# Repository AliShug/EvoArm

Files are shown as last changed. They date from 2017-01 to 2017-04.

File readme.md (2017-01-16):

EvoArm is an open-source, 3D-printable, desktop-sized, 3+2DOF robot arm design which uses serially controlled Dynamixel smart servos. It is based in part on the [LiteArm i2](http://www.thingiverse.com/thing:480446) design by "Armatec".

[Licensed under CC-BY-SA 3.0](https://creativecommons.org/licenses/by/3.0/)

## Core Action
Swing | Main Arm | Actuator/Forearm
--- | --- | ---
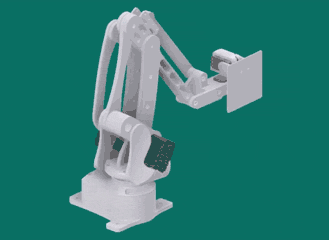
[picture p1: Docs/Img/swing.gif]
Swing GIF
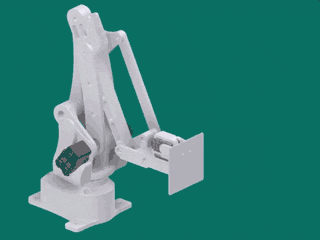
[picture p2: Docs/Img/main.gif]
Main GIF
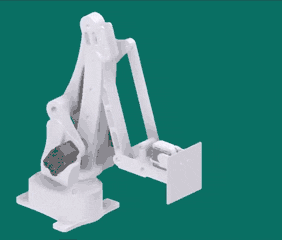
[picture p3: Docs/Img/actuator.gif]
Actuator GIF
 |  | 

The arm is actuated using 3 Dynamixel smart servos, either the [AX-12 or 18A](http://support.robotis.com/en/product/actuator/dynamixel/dxl_ax_main.htm), which both have identical casings and control protocols - I recommend using AX-18A motors, as the 12s are a bit underpowered.

## Effector
The design presented here has a flat touchpad actuated using 2 Dynamixel [XL-320](http://support.robotis.com/en/product/actuator/dynamixel_x/xl_series/xl-320.htm) servos, providing an additional 2DOF at the arm's "wrist". The design inherently keeps the base wrist joint level with the floor.

## Inverse Kinematics
The inverse kinematics application is written in Python with [PyGame](http://pygame.org/hifi.html), and takes the form of a graphical control app which also accepts simple streamed commands from other programs via UDP. It serves the purpose of calculating the desired target servo positions for the arm, given a 3D target position and orientation for the end-effector. It also provides linear interpolation on the target position and basic bounds-checking to prevent self-interference on the motors or mechanical failure of the design (the reachable volume is visualised in green).

Start the application with `python PyIK` from the root directory. Unfortunately the application may not be usable on smaller screens, since the size is fixed. To enable control, press the spacebar, and watch the command window in which the app was started for additional information.

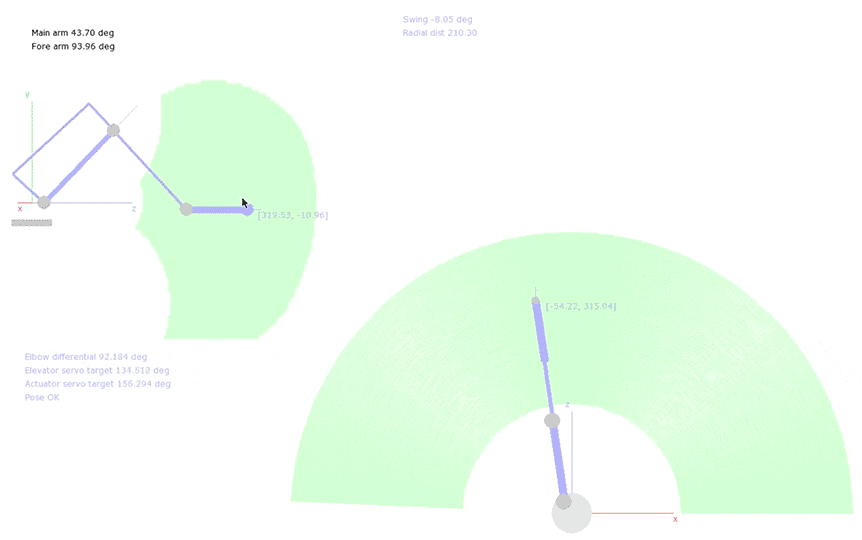
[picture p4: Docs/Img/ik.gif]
Inverse Kinematics program


The IK app is configured to connect to the arm through a properly configured Arduino Mega2560 controller, from a Windows machine. More details to come!

## Hardware
The current system interfaces with the servos using an Arduino Mega2560, which provides multiple hardware UARTs in addition to the one used for PC/Arduino communications. The AX and XL series servos use different control protocols, so they are connected to the Arduino on physically separate lines, with one UART Tx/Rx pair for each *set* of servos. Since the servos use only a single (synchronous) data line, the Tx/Rx lines are multiplexed using a 74LS241 tri-state buffer. The multiplexing is controlled using an additional transmit enable line from the Arduino.

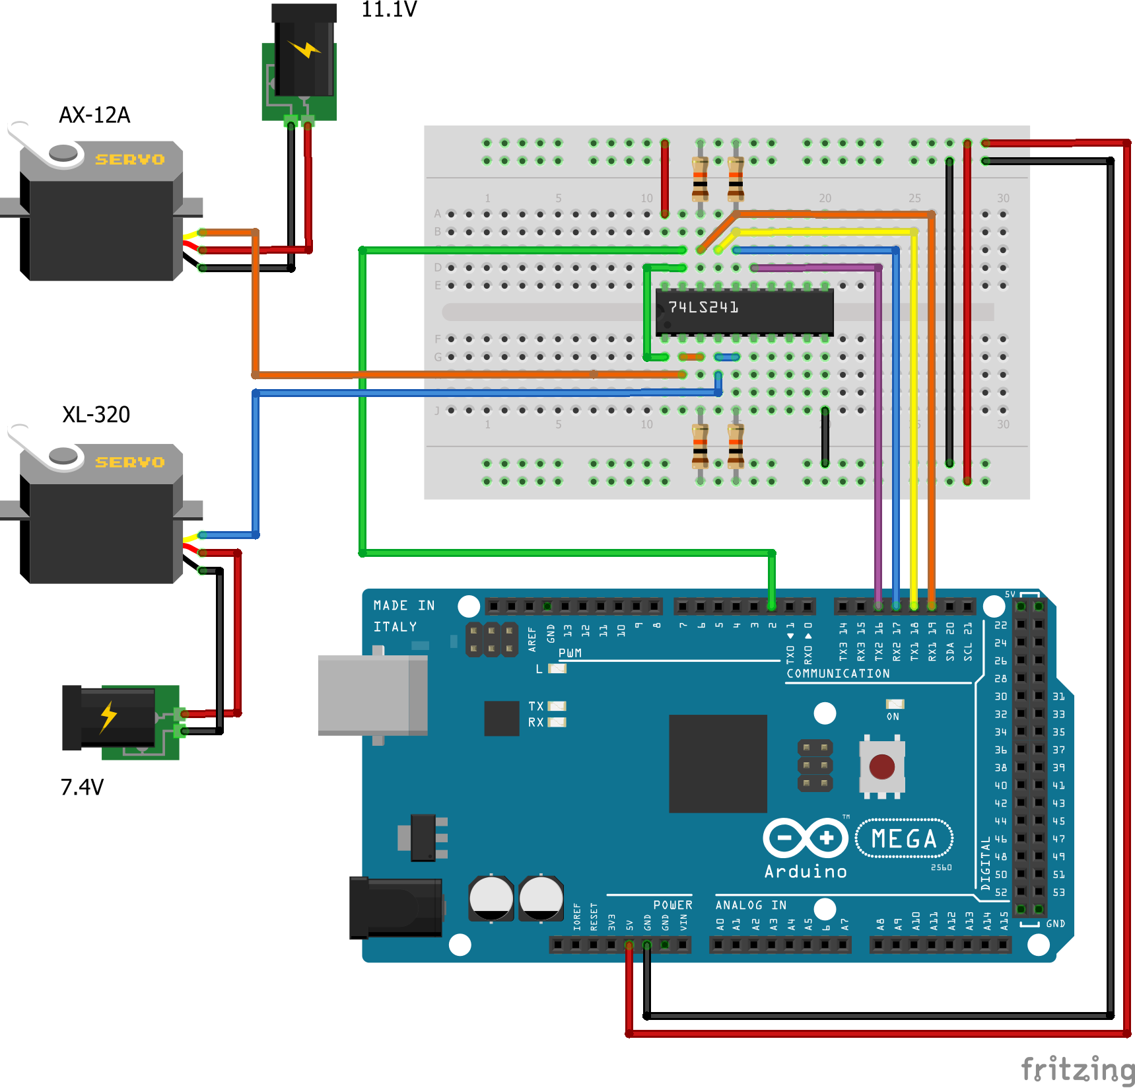
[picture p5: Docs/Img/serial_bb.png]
Breadboard diagram of hardware


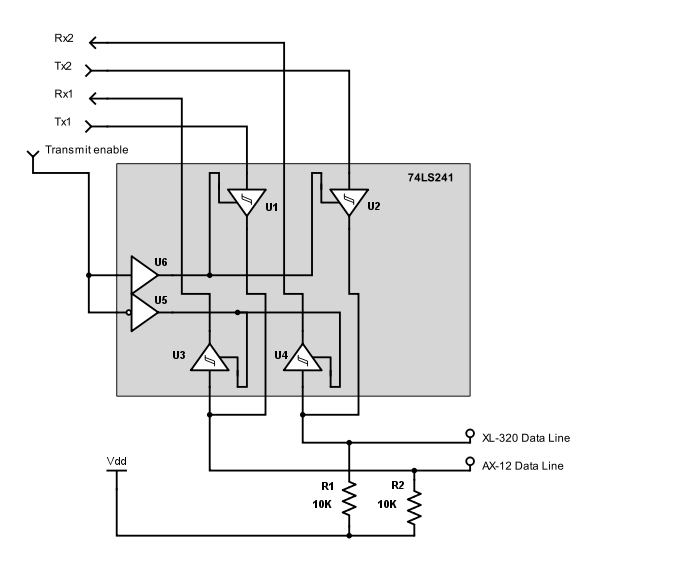
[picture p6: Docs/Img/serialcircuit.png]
Circuit diagram of serial communications
  

The data lines should be pulled high (to +5V) to stop them from "floating" while not in use.

Experimentally, it's possible to interface with these servos using only an Arduino Uno (or equivalent, e.g. Arduino Nano), without preventing the use of the single hardware UART for PC/Arduino communications. The ATMega328p in those boards is clocked high enough to allow basic *software-based* synchronous serial at 1 megabaud, using only one pin for each data line, and *no additional hardware*. The downside is interfering with the interrupts on the board, which can break some of the normal Arduino timing routines. If all you want to do is communicate with the servos from a PC, this doesn't matter. I'll explore this option further when I have the chance.

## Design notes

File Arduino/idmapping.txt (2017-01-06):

ModelNumber : 0x00
FirmwareVersion : 0x01
ID : 0x02
ReturnDelay : 0x03
CWLimit : 0x04
CCWLimit : 0x05
TempLimit : 0x06
LowVoltageLimit : 0x07
HighVoltageLimit : 0x08
MaxTorque : 0x09
MaxTorque : 0x0A
AlarmFlags : 0x0B
ShutdownFlags : 0x0C
TorqueEnable : 0x0D
LED : 0x0E
Voltage : 0x0F
Position : 0x10
Load : 0x11
Temperature : 0x12
Speed : 0x13
GoalPosition : 0x14
GoalSpeed : 0x15
TorqueLimit : 0x16
CWMargin : 0x17
CCWMargin : 0x18
CWSlope : 0x19
CCWSlope : 0x1A
Punch : 0x1B
Moving : 0x1C

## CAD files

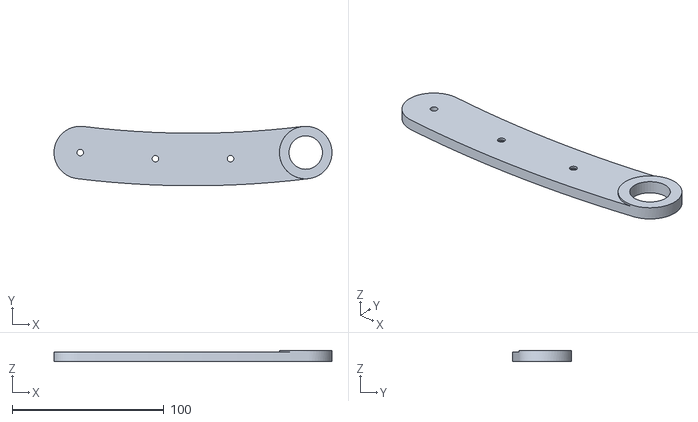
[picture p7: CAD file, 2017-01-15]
Design/Arm - main arm R.stl
183.0 x 39.1 x 7.00

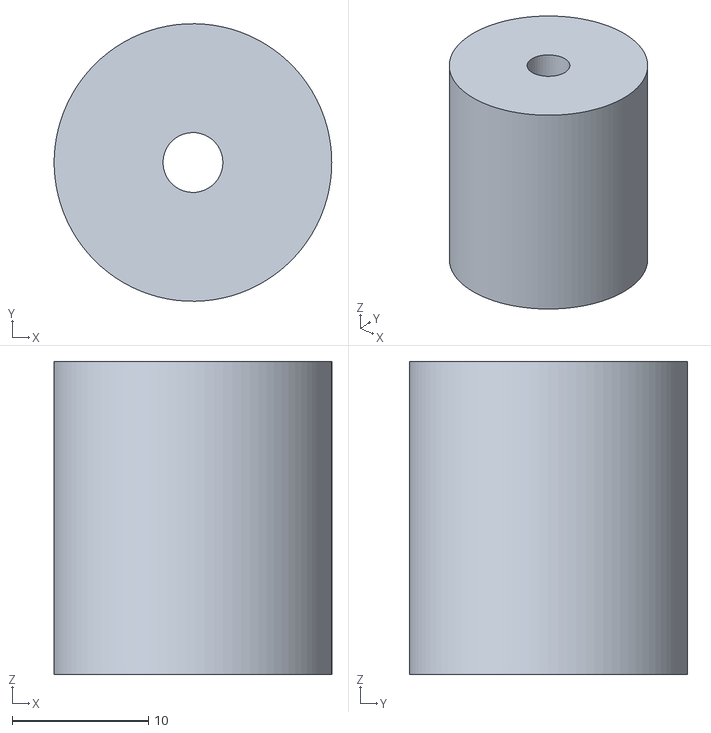
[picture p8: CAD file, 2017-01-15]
Design/Arm - main arm spacer.stl
20.4 x 20.4 x 23.0

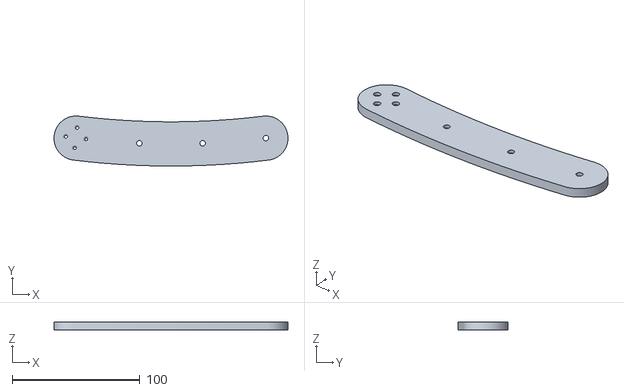
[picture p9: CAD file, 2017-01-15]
Design/Arm - main arm L.stl
183.0 x 39.1 x 6.00

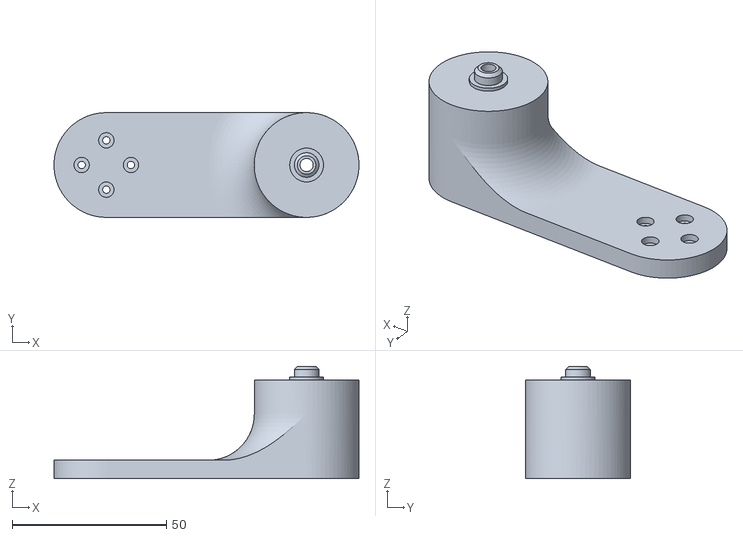
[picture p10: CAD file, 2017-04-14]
Design/Arm - actuator hinge R.stl
99.0 x 34.0 x 36.5

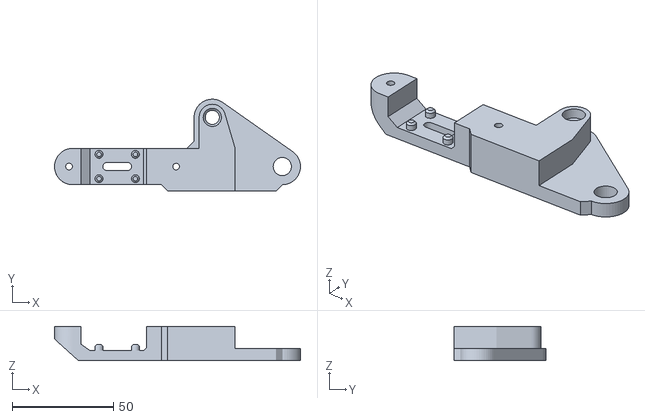
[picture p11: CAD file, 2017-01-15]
Design/Derived Parts/Arm - effector right v2.stl
121.6 x 45.3 x 17.0

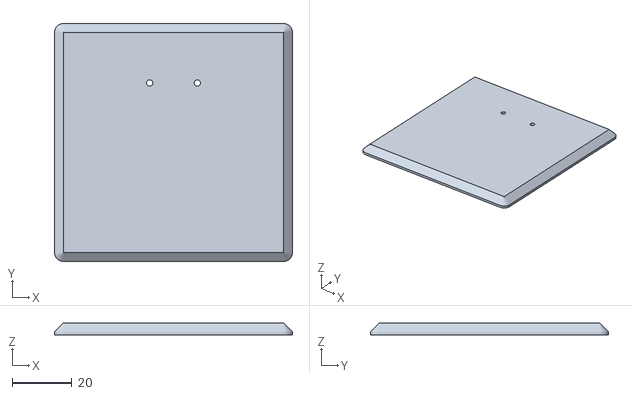
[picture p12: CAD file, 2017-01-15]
Design/Effector/Touchplate.stl
80.0 x 80.0 x 4.00

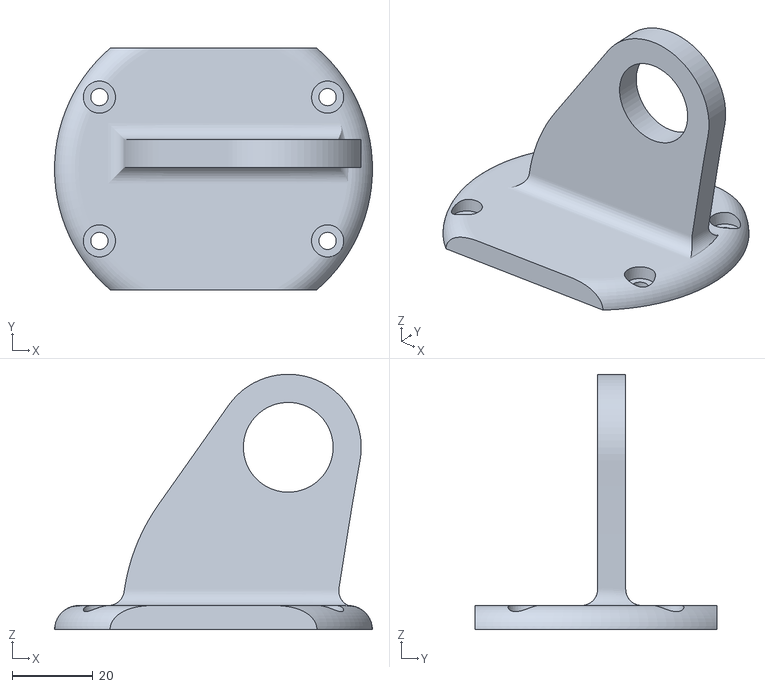
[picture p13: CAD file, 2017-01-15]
Design/Arm - base center support.stl
79.0 x 60.0 x 63.4

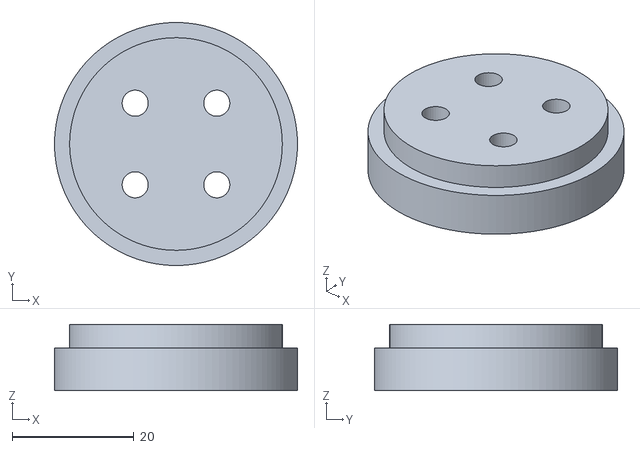
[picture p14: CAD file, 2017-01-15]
Design/Derived Parts/Base Shaft.stl
40.0 x 40.0 x 10.9

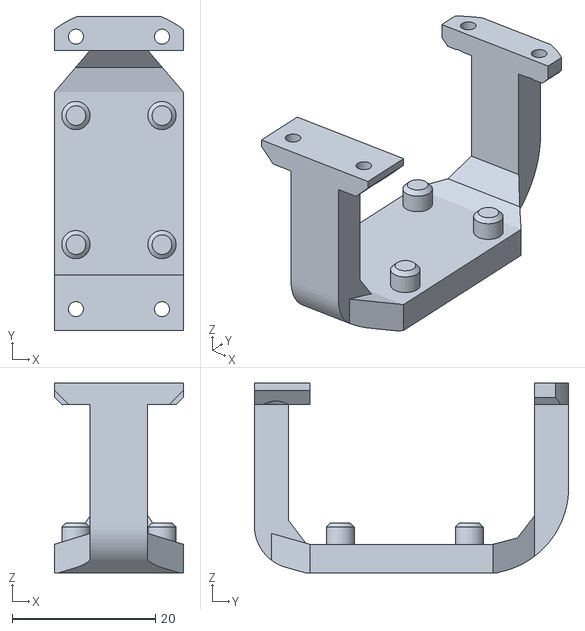
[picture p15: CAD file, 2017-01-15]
Design/Effector/Joint Upper.stl
18.0 x 43.8 x 26.5

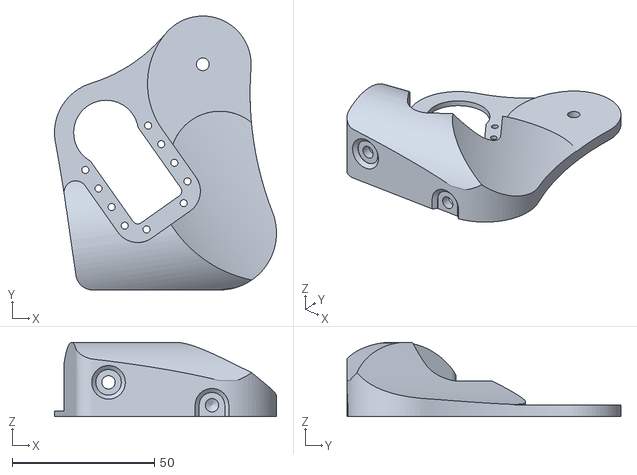
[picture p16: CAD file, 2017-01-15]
Design/Arm - shoulder L.stl
78.0 x 96.3 x 26.1

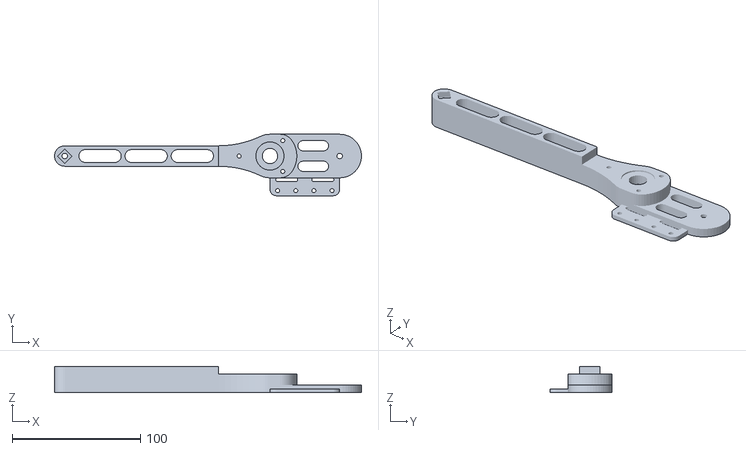
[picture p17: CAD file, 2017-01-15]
Design/Derived Parts/Arm - forearm v2 1.stl
239.4 x 48.0 x 20.6

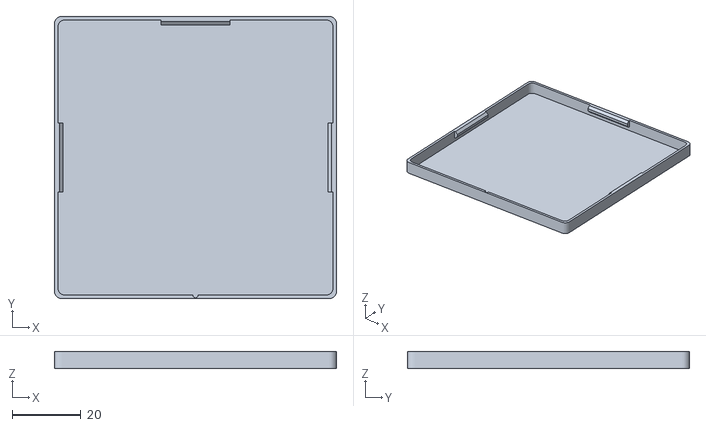
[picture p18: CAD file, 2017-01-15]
Design/Effector/Cap plate.stl
82.0 x 82.0 x 5.00

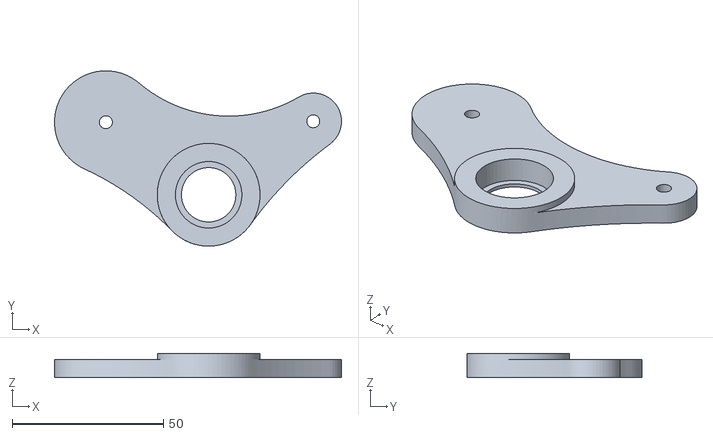
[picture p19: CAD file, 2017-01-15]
Design/Arm - parallel hinge.stl
94.9 x 58.0 x 8.00

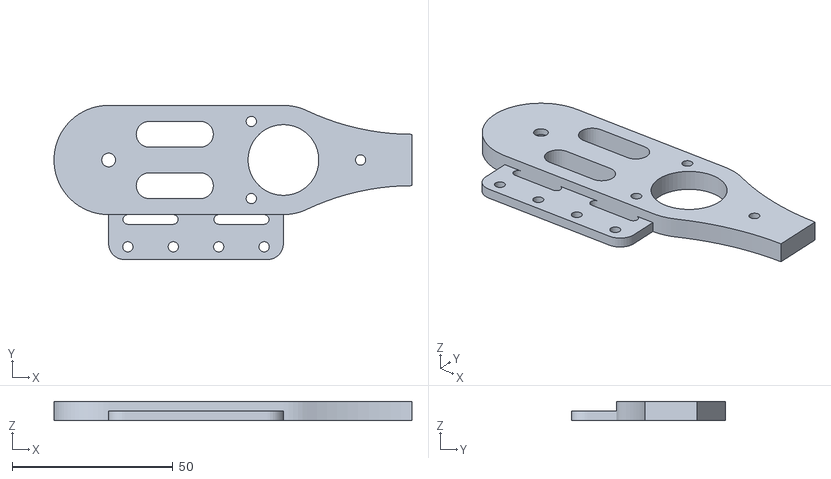
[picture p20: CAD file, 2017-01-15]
Design/Derived Parts/Arm - forearm v2 2.stl
111.4 x 48.0 x 6.00

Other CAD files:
Design/Effector/Joint Lower.stl
Design/Arm - actuator linkage.stl
Design/Derived Parts/Base Plate.stl
Design/Derived Parts/Effector - Hinge 1.stl
Design/Arm - 608 bearing cap [Med].ipt
Design/Arm - 608 bearing cap [Med].stl
Design/Arm - 608 bearing cap [Small].ipt
Design/Arm - 608 bearing cap [Small].stl
Design/Arm - actuator hinge L.ipt
Design/Arm - actuator hinge L.stl
Design/Arm - actuator hinge R.ipt
Design/Arm - actuator linkage.ipt
Design/Arm - base center support.ipt
Design/Arm - effector base v2.ipt
Design/Arm - effector hinge.ipt
Design/Arm - effector joint.ipt
Design/Arm - forearm v2 hinge.ipt
Design/Arm - forearm v2 hinge.stl
Design/Arm - forearm v2.ipt
Design/Arm - main arm L.ipt
Design/Arm - main arm R.ipt
Design/Arm - main arm spacer.ipt
Design/Arm - mounting bottom.ipt
Design/Arm - mounting bottom.stl
Design/Arm - mounting top.ipt
Design/Arm - mounting top.stl
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

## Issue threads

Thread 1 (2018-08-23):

Error Regarding File PyIK.py from PyIk/src/PyIK.py

nayanleo, 2018-08-23:
hie AliShug,
       I refered your code and trying to use in my system(UBUNTU 14.04). when I compile PyIK.py file  I'm getting Error as follows:

No 'Logs/' folder available: Performance logging disabled
Warning: shoulder servo not connected
Warning: elbow servo not connected
Warning: wrist_y servo not connected
Warning: wrist_x servo not connected
Warning: swing servo not connected
Rendering reachable volume...
Note: Spacebar toggles movement enable/disable
Traceback (most recent call last):
  File "PyIK.py", line 413, in <module>
    app.tick()
  File "PyIK.py", line 361, in tick
    self.tickComms()
  File "PyIK.py", line 223, in tickComms
    self.sockOut.send(self.arm.getIKPose().serialize() + sensor)
socket.error: [Errno 111] Connection refused

since i'm trying to solve these errors but can you please explain why this happens.
 Regards me,
As early as possible.

Closed 2018-08-30.

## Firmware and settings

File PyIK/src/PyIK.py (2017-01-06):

from __future__ import print_function

import sys
import time
import serial
import socket
import select
import struct

import numpy as np
import pygame as pyg

from pid import PIDControl
import Protocol
from solvers import IKSolver, PhysicalSolver
import window
import views
import litearm
import capsense
import armvolume

from util import *

RECV_PORT = 14001
TRAN_PORT = 14002

MAX_SPEED = 800.0
ACCEL = 1600.0
DECEL = 1.0

CS_PORT = 'COM4'

WINDOW_W = 1280
WINDOW_H = 800

import pdb;

class Kinectics:
    def findSerial(self):
        ports = ['COM{0}'.format(i+1) for i in range(256)]
        results = []
        for port in ports:
            try:
                comm = serial.Serial(port)
                comm.close()
                results.append(port)
            except (OSError, serial.SerialException):
                pass
        if len(results) > 0:
            return results[0]
        else:
            print ("No valid serial port found")
            return None

    def connectController(self):
        port = 'COM3'
        try:
            return Protocol.serialConnect(port, 250000)
        except:
            return None

    def findServos(self, comm):
        """Retrieves and processes the list of available (responsive) servos
        attached to the arm's Arduino controller. Returns a dictionary mapping
        from servo functions to Servo() objects, or None if no matching servo
        was found for a particular function"""
        servos = {
            'swing': None,
            'actuator': None,
            'shoulder': None,
            'wrist_x': None,
            'wrist_y': None
        }
        # Mapping of IDs->functions
        v1_IDs = {
            0 : 'swing',
            1 : 'actuator',
            2 : 'shoulder'
        }
        v2_IDs = {
            1 : 'wrist_x',
            0 : 'wrist_y'
        }
        # Servos retrieved from Arduino
        found = Protocol.findServos(comm)
        i = 0
        for v1servo in found['v1']:
            servos[v1_IDs[i]] = v1servo
            i += 1
        j = 0
        for v2servo in found['v2']:
            servos[v2_IDs[j]] = v2servo
            j += 1
        # Return our output servo dictionary
        return servos

    def __init__(self):
        self.stopped = False

        # Bind our comms socket
        self.bindSocket()

        # Performance tracking
        self.ik_time_accum = 0
        self.ik_time_counter = 0
        self.render_time_accum = 0
        self.render_time_counter = 0
        self.serial_time_accum = 0
        self.serial_time_counter = 0
        try:
            self.perflog = open('Logs/{0}.perflog'.format(time.time()), 'w')
        except IOError as e:
            print("No 'Logs/' folder available: Performance logging disabled")
            self.perflog = None
        self.time_start = time.clock()

        # Find the available servos through the attached board
        comm = self.connectController()
        self.servos = self.findServos(comm)


        window.InitRenderer()
        self.r = window.Renderer(pyg.display.set_mode([WINDOW_W, WINDOW_H], pyg.DOUBLEBUF|pyg.HWSURFACE))
        pyg.display.set_caption("IK Control Test")

        # The arm's controller - encapsulates IK and arm control
        self.arm = litearm.ArmController(
            servo_swing = self.servos['swing'],
            servo_shoulder = self.servos['shoulder'],
            servo_elbow = self.servos['actuator'],
            servo_wrist_x = self.servos['wrist_x'],
            servo_wrist_y = self.servos['wrist_y'],
            # use the default config
            arm_config = litearm.ArmConfig())

        # Capacitive sensor on connected UNO
        try:
            self.capSense = capsense.CapacitiveSensor(CS_PORT)
        except serial.SerialException as ex:
            self.capSense = None;

        self.sideView = views.PlaneView(width=10)
        self.realSideView = views.PlaneView(width=5, color=gray, positioning='offset')
        self.topView = views.TopView(width=12)
        self.realTopView = views.TopView(width=6, color=gray, positioning='offset')

        self.arm.pollServos()
        realPose = self.arm.getRealPose()
        if realPose is not None:
            self.curGoal = self.arm.getRealPose().effector
        else:
            self.curGoal = np.array([0., 50., 200.])
        self.ikTarget = np.array(self.curGoal)
        self.lastValidGoal = np.array(self.curGoal)
        self.curDir = [0.0, 0.0]
        self.goalNormal = [0, 0, 1]
        self.ikOffset = np.array([0.,0.,0.])

        self.lerpSpeed = 0
        self.lerpTimer = time.clock()
        self.lastPose = None

        # render the reachable area
        print("Rendering reachable volume...")
        self.reachableVolume = armvolume.ArmVolume(self.arm)
        self.sideView.renderReachableVolume(self.reachableVolume)

        print("Note: Spacebar toggles movement enable/disable")

    def stop(self):
        self.arm.enableMovement(False)
        if self.perflog is not None:
            self.perflog.write('ik_avg {0}\n'.format(self.ik_time_accum/self.ik_time_counter))
            self.perflog.write('serial_avg {0}\n'.format(self.serial_time_accum/self.serial_time_counter))
            self.perflog.write('render_avg {0}\n'.format(self.render_time_accum/self.render_time_counter))
            self.perflog.write('runtime {0}\n'.format(time.clock()-self.time_start))
            self.perflog.close()
        self.sockIn.close()
        self.sockOut.close()
        pyg.quit()
        self.stopped = True;

    def bindSocket(self):
        # We use UDP (datagrams) since we don't really care if the messages
        # arrive - just transmit and hope for the best
        self.sockIn = socket.socket(socket.AF_INET, socket.SOCK_DGRAM)
        self.sockOut = socket.socket(socket.AF_INET, socket.SOCK_DGRAM)
        self.sockIn.bind(('localhost', RECV_PORT))
        self.sockOut.connect(('localhost', TRAN_PORT))

    def tickComms(self):
        """(Socket comms) Check for incoming datagrams and send our updates"""
        while len(select.select([self.sockIn],[],[],0)[0]) > 0:
            # Ready to receive
            try:
                raw = self.sockIn.recv(4096)
                data = struct.unpack('?ffffff', raw)
                # enable or disable the physical arm
                # goal change is only applied with an enabled packet
                self.arm.enableMovement(data[0])
                if data[0]:
                    goalPos = np.array(data[1:4])
                    self.goalNormal = np.array(data[4:])
                    #print(data)
                    newGoal = goalPos*1000
                    self.curGoal = np.array(newGoal)
            except socket.error as err:
                print ("Socket error: {0}".format(err))
        #sensor = struct.pack('i', 0)
        if self.capSense:
            self.capSense.updateReadings()
            val = self.capSense.latest()
            try:
                sensor = struct.pack('i', int(self.capSense.latest()))
            except:
                sensor = '\0\0\0\0'
        else:
            sensor = '\0\0\0\0'
        realPose = self.arm.getRealPose()
        if realPose is not None:
            self.sockOut.send(realPose.serialize() + sensor)
        else:
            self.sockOut.send(self.arm.getIKPose().serialize() + sensor)

    def resetIKTarget(self, target):
        # Reset lerp timer
        self.lerpTimer = time.clock()
        # Reset lerp speed to 0
        self.lerpSpeed = 0.0
        # Clear error buildup
        self.arm.clearPositionError()
        # Set the IK target
        self.ikTarget = np.array(target)

    def lerpIKTarget(self):
        # Scales with time delta
        now = time.clock()
        dt = now - self.lerpTimer
        self.lerpTimer = now

        delta = np.subtract(self.curGoal, self.ikTarget)
        dist = np.linalg.norm(delta)
        if (dist < 1):
            self.lerpSpeed = ACCEL*0.03
            return
        else:
            # acceleration
            self.lerpSpeed += ACCEL*dt
            curMax = MAX_SPEED*(0.03 + 0.97*min(1, 0.01*DECEL*dist))
            if self.lerpSpeed > curMax:
                self.lerpSpeed = curMax
            self.ikTarget = self.ikTarget + normalize(delta)*min(dist, dt*self.lerpSpeed)
        # Disable motor error checks at high speeds
        if self.lerpSpeed > 0.11*ACCEL:
            self.arm.clearPositionError()


    def getGoalOffset(self):
        """3D Offset between measured position and goal position"""
        pose = self.arm.getRealPose()
        return np.subtract(self.ikTarget, pose.effector)

    def tick(self):
        if self.stopped:
            return

        # Polling/update loop
        for event in pyg.event.get():
            if event.type == pyg.QUIT:
                self.stop()
                return
            elif (event.type == pyg.MOUSEBUTTONDOWN
                    or event.type == pyg.MOUSEMOTION):
                if pyg.mouse.get_pressed()[0]:
                    if event.pos[0] < (420 + views.ORIGIN_L[0]) and event.pos[1] < event.pos[0]*2:
                        # lock direction on start of interaction
                        if event.type == pyg.MOUSEBUTTONDOWN:
                            goal_topdown = [self.curGoal[0], self.curGoal[2]]
                            self.curDir = normalize(goal_topdown)
                        sidegoal = views.unpt_l(event.pos)
                        radial = sidegoal[0]
                        if radial < 1:
                            radial = 1
                        vec = radial * self.curDir
                        self.curGoal[0] = vec[0]
                        self.curGoal[1] = sidegoal[1]
                        self.curGoal[2] = vec[1]
                    else:
                        topgoal = views.unpt_r(event.pos)
                        self.curGoal[0] = topgoal[0]
                        self.curGoal[2] = topgoal[1]
                    if self.curGoal[2] < 1:
                        self.curGoal[2] = 1
            elif event.type == pyg.KEYUP:
                if event.key == pyg.K_SPACE:
                    if self.arm.motion_enable:
                        self.arm.enableMovement(False)
                    else:
                        self.arm.enableMovement(True)

        # Clear the render canvas
        self.r.surf.fill(white)

        # If arm is active, we lerp towards target.
        # Otherwise we set the IK target to match the current pose
        if self.arm.motion_enable:
            self.lerpIKTarget()
        else:
            real_pose = self.arm.getRealPose()
            if real_pose is not None:
                self.resetIKTarget(real_pose.effector)

        # IK - calculate swing and elbow pos using goal pos
        timer = time.clock()
        self.arm.setWristGoalPosition(self.ikTarget)
        self.arm.setWristGoalDirection(self.goalNormal)
        self.ik_time_accum += time.clock()-timer
        self.ik_time_counter += 1

        pose = self.arm.getIKPose()

        # Find the current servo positions
        self.arm.pollServos()

        # Make sure we're good
        if pose is None or not pose.checkClearance():
            # Revert to last good goal position
            #self.curGoal = np.array(self.lastValidGoal)
            # Find an acceptible position
            #pdb.set_trace()
            self.ikTarget = self.reachableVolume.projectValid(self.arm, self.ikTarget)
            #printVec(self.ikTarget)
            self.arm.setWristGoalPosition(self.ikTarget)
            pose = self.arm.getIKPose()

        # Calculate pose
        if self.lastPose is None:
            self.lastPose = pose
        display_pose = self.lastPose

        # Update display pose
        display_pose = pose
        self.lastPose = pose
        # Drive the main arm
        self.arm.setTargetPose(pose)
        timer = time.clock()
        self.arm.tick()
        self.serial_time_accum += time.clock()-timer
        self.serial_time_counter += 1
        # Update the last known valid goal
        self.lastValidGoal = np.array(self.ikTarget)

        # Update the views
        realPose = self.arm.getRealPose()
        self.drawViews(display_pose)
        if realPose is not None:
            self.realSideView.draw(realPose, self.r)
            self.realTopView.draw(realPose, self.r)
        pyg.display.flip()

        self.tickComms()

    def displayServoPositions(self, col, pos):
        i = 0
        for (name,servo) in self.servos.iteritems():
            if servo is None:
                continue
            text = "{name} [{id}]: {d:.3f} deg".format(
                name = name,
                d = servo.data['pos'],
                id = servo.id)
            self.r.drawText(text, col, [pos[0], pos[1]+i*20])
            i += 1

    def drawViews(self, pose):
        timer = time.clock()

        # Find the reachable arc for this height
        arc = self.reachableVolume.getRadii(pose.effector[1])
        if arc[1] is not None:
            self.topView.setReachableArc(int(arc[0]), int(arc[1]))
        else:
            self.topView.setReachableArc(0, 0)

        self.sideView.drawBack(pose, self.r)
        self.topView.drawBack(pose, self.r)
        self.sideView.draw(pose, self.r)
        self.topView.draw(pose, self.r)
        # Display critical pose angles
        text = "Elbow differential {0:.3f} deg".format(pose.armDiffAngle())
        self.r.drawText(text, blue if pose.checkDiff() else red, [40, 520])

        text = "Elevator servo target {0:.3f} deg".format(pose.getServoElevator())
        self.r.drawText(text, blue if pose.checkElevator() else red, [40, 540])

        text = "Actuator servo target {0:.3f} deg".format(pose.getServoActuator())
        self.r.drawText(text, blue if pose.checkActuator() else red, [40, 560])

        if pose.checkPositioning():
            self.r.drawText("Pose OK", blue, [40, 580])
        else:
            self.r.drawText("Pose Invalid", red, [40, 580])
        # Display servo positions
        self.displayServoPositions(black, [400, 20])
        # Store the render timing
        self.render_time_accum += time.clock() - timer
        self.render_time_counter += 1


if __name__ == "__main__":
    app = Kinectics()
    while not app.stopped:
        app.tick()

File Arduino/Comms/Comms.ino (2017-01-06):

/*
 Name:		Comms.ino
 Created:	4/26/2016 4:55:32 PM
 Author:	alist
*/

#include <CapacitiveSensor.h>

#include "Protocol.h"
#include <DX1Motor.h>
#include <DX2Motor.h>


#define BUFFER_LEN 1024

bool waitTimeout(Stream &s, unsigned long wait) {
    unsigned long start = millis();

    do {
        if (s.peek() >= 0) {
            return true;
        }
    } while (millis() - start < wait);

    return false;
}

DX1Motor x1Servos[10];
DX2Motor x2Servos[10];
int nx1 = 0;
int nx2 = 0;

// Init - Find servos
void setup() {
    pinMode(2, OUTPUT);
    digitalWrite(2, 0);

    DX1Motor::Init(DX1MOTOR_BAUD_1MBS, 2);
    DX2Motor::Init(DX2MOTOR_BAUD_1MBS, 2);
    Serial.begin(250000);
    while (!Serial);

    // Fill out our servo listings
    // LED blinks at start and finish
    pinMode(13, OUTPUT);
    digitalWrite(13, LOW);
    delay(100);
    digitalWrite(13, HIGH);

    for (int checkid = 0; checkid < 252; checkid++) {
        DX1Motor servo(checkid);
        int err;

        if (servo.getID(err), err == DX1MOTOR_ERR_OK) {
            x1Servos[nx1++] = servo;
            /*servo.setCWLimit(0.0f);
            servo.setCCWLimit(300.0f);
            delay(10);*/
        }
    }
    for (int checkid = 0; checkid < 252; checkid++) {
        DX2Motor servo(checkid);
        int err;

        if (servo.getID(err), err == DX2MOTOR_ERR_OK) {
            x2Servos[nx2++] = servo;
            servo.setCWLimit(0.0f);
            servo.setCCWLimit(300.0f);
            servo.setControlMode(2);
        }
    }

    // Low latency
    for (int i = 0; i < nx1; i++) {
        x1Servos[i].setReturnLevel(1);
        x1Servos[i].setReturnDelay(0);
    }
    for (int i = 0; i < nx2; i++) {
        x2Servos[i].setReturnDelay(0);
    }
    
    digitalWrite(13, LOW);
    delay(500);
    digitalWrite(13, HIGH);

    CapacitiveSensor capSense(30, 31);

    Serial.println("CommTest READY");

    Protocol protocol(x1Servos, nx1, x2Servos, nx2);
    while (true) {
        // Execute protocol
        protocol.handleIncoming(Serial);
    }
}

void loop() {}

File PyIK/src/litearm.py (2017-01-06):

from __future__ import print_function

import numpy as np
import struct

import solvers
import pid
from util import *

MOTORSPEED = 0.9
MOTORMARGIN = 1
MOTORSLOPE = 30

ERRORLIM = 5.0

class ArmConfig:
    """Holds an arm's proportions, limits and other configuration data"""
    def __init__(self,
                 main_length = 148.4,
                 forearm_length = 160,
                 linkage_length = 155,
                 lower_actuator_length = 65,
                 upper_actuator_length = 54.4,
                 wrist_length = 90.52,
                 shoulder_offset = [-9.7, 18.71]):
        self.main_length = main_length
        self.forearm_length = forearm_length
        self.linkage_length = linkage_length
        self.lower_actuator_length = lower_actuator_length
        self.upper_actuator_length = upper_actuator_length
        self.wrist_length = wrist_length;
        self.shoulder_offset = shoulder_offset


class ArmPose:
    """
    Defines a physical configuration of a LiteArm robot arm.
    Internal angles are relative to vertical (elevator/actuator) or straight
    forward (swing), and are stored in radians. Extracted servo angles range
    0-300 and are measured in degrees.

    Provides methods for:
        - finding the required servo angles to reach the pose
        - checking the validity of the pose
    """
    structFormat = 'fffff'

    @staticmethod
    def calcElevatorAngle(servoAngle):
        return radians(178.21 - servoAngle)

    @staticmethod
    def calcSwingAngle(servoAngle):
        return radians(150.0 - servoAngle)

    @staticmethod
    def calcActuatorAngle(servoAngle):
        return radians(servoAngle - 204.78)

    @staticmethod
    def calcWristXAngle(servoAngle):
        return radians(150.0 - servoAngle)

    @staticmethod
    def calcWristYAngle(servoAngle):
        return radians(servoAngle - 147.0)

    def __init__(self,
                 arm_config,
                 swing_angle,
                 shoulder_angle,
                 actuator_angle,
                 elbow_angle,
                 elbow2D,
                 wrist2D,
                 effector2D,
                 effector,
                 wrist_x,
                 wrist_y):
        self.cfg = arm_config
        self.swing_angle = swing_angle
        self.shoulder_angle = shoulder_angle
        self.actuator_angle = actuator_angle
        self.elbow_angle = elbow_angle
        # Joints in the arm
        shoulder = rotate(self.cfg.shoulder_offset, swing_angle)
        self.shoulder2D = [self.cfg.shoulder_offset[1], 0]
        self.shoulder = [shoulder[0], 0, shoulder[1]]
        self.wrist2D = wrist2D
        self.effector2D = effector2D
        self.effector = effector
        # Construct the 3D elbow & wrist positions from the 2D (planar) IK
        # solution
        arm_vec = effector - self.shoulder
        arm_vec[1] = 0
        self.elbow2D = elbow2D
        self.elbow = self.shoulder + normalize(arm_vec)*elbow2D[0]
        self.elbow[1] = elbow2D[1]
        self.wrist = self.effector - normalize(arm_vec)*arm_config.wrist_length
        # Wrist pose
        self.wristXAngle = wrist_x
        self.wristYAngle = wrist_y

    def getServoElevator(self):
        return 178.21 - degrees(self.shoulder_angle)

    def getServoActuator(self):
        return degrees(self.actuator_angle) + 204.78

    def getServoSwing(self):
        return 150 - degrees(self.swing_angle)

    def getServoWristX(self):
        return 150 - degrees(self.wristXAngle)

    def getServoWristY(self):
        return 147 + degrees(self.wristYAngle)

    def armDiffAngle(self):
        return degrees(self.shoulder_angle - self.actuator_angle)

    def checkActuator(self):
        angle = self.getServoActuator()
        return angle >= 95 and angle <= 250

    def checkDiff(self):
        angle = self.armDiffAngle()
        return angle >= 44 and angle <= 175

    def checkElevator(self):
        angle = self.getServoElevator()
        return angle >= 60 and angle <= 210

    def checkForearm(self):
        angle = degrees(self.elbow_angle + self.shoulder_angle)
        return angle < 200 and angle > 80

    def checkSwing(self):
        angle = self.getServoSwing()
        return angle >= 60 and angle <= 240

    def checkWristX(self):
        angle = self.getServoWristX()
        return angle >= 60 and angle <= 240

    def checkWristY(self):
        angle = self.getServoWristY()
        return angle >= 60 and angle <= 160

    def checkPositioning(self):
        # When Y>0 Forearm always faces outwards
        if self.wrist2D[1] > 0 and self.wrist2D[0] < self.elbow2D[0]:
            return False
        # No valid positions X<=0
        if self.wrist2D[0] <= 0:
            return False
        # Effector height range
        if self.effector[1] > 180 or self.effector[1] < -200:
            return False
        return True

    def checkClearance(self):
        return (self.checkDiff() and self.checkActuator() and
                self.checkElevator() and self.checkSwing() and
                self.checkWristX() and self.checkWristY() and
                self.checkPositioning() and self.checkForearm())

    def serialize(self):
        """Returns a packed struct holding the pose information"""
        return struct.pack(
            ArmPose.structFormat,
            self.swing_angle,
            self.shoulder_angle,
            self.elbow_angle,
            self.wristXAngle,
            self.wristYAngle
        )
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

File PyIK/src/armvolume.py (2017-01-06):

import numpy as np

from util import *

class ArmVolume:
    def __init__(self, arm, res=100, offset=90, backSize=500):
        self.offset = offset
        self.res = res
        self.samples = np.ndarray(shape=(res,res), dtype=bool)
        self.size = (430-offset, backSize)

        self.y_step = self.size[1]/float(res)
        self.x_step = self.size[0]/float(res)
        for y in xrange(res):
            for x in xrange(res):
                pos = [0, (y-res/2)*self.y_step, offset + x*self.x_step]
                self.samples[x,y] = self.trueValid(arm, pos)

    def getRadii(self, height):
        y_ind = np.clip(int(height/self.y_step + self.res/2), 0, self.res-1)

        min = 0
        max = None
        for x in xrange(self.res):
            if max is None:
                if not self.samples[x, y_ind]:
                    min = self.offset + x*self.x_step
            if self.samples[x, y_ind]:
                max = self.offset + x*self.x_step

        return min,max

    def isValid(self, point):
        """Whether or not a potential end-effector position is likely to be
        valid. Point must be 2D (in IK plane)
        """
        x = int((point[0]-self.offset)/self.x_step)
        y = int(point[1]/self.y_step)
        return self.samples[x, y]

    def trueValid(self, arm, point):
        arm.setWristGoalPosition(point)
        if arm.ik.valid:
            pose = arm.getIKPose()
            if pose is not None:
                test = pose.checkClearance()
            else:
                test = False
        else:
            test = False
        return test


    def projectValid(self, arm, point):
        """Projects an invalid point to a valid one"""
        point = np.array(point)
        # 3D projection target point in plane
        td = normalize([point[0], point[2]])*300
        proj = np.array([td[0], 0, td[1]])
        point += (proj - point)*0.005

        iters = 0
        while not self.trueValid(arm, point) and iters < 1000:
            point += (proj - point)*0.005
            iters += 1
        return point

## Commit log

2016-12-28 Inventor Design files
    Parts and assembly were saved with Autodesk Inventor 2017.
    [608-inner.ipt, 608-outer.ipt, 6082RS.iam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]
2017-01-15 Export files for printing
    [Arm - 608 bearing cap [Med].ipt, Arm - 608 bearing cap [Med].stl, Arm - 608 bearing cap [Small].ipt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]
2017-01-16 Notes/diagrams of hardware setup
    Includes Fritzing layout
    [Arm - main arm spacer.ipt, serial.fzz]
2017-01-30 Improve base design
    [Arm - mounting bottom.ipt, Full.iam]
2017-04-14 Design changes, working on new base
    [Arm - actuator hinge R.ipt, Arm - actuator hinge R.stl, Arm - mounting v2.ipt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]
2017-06-18 New slew column
    [Arm - mounting v2.ipt, Arm - slew column A.ipt, Arm - slew column B.ipt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]
2017-07-03 Align slew rotation
    [Arm - mounting v2.ipt, Arm - slew column C.ipt, New mounting.iam]
